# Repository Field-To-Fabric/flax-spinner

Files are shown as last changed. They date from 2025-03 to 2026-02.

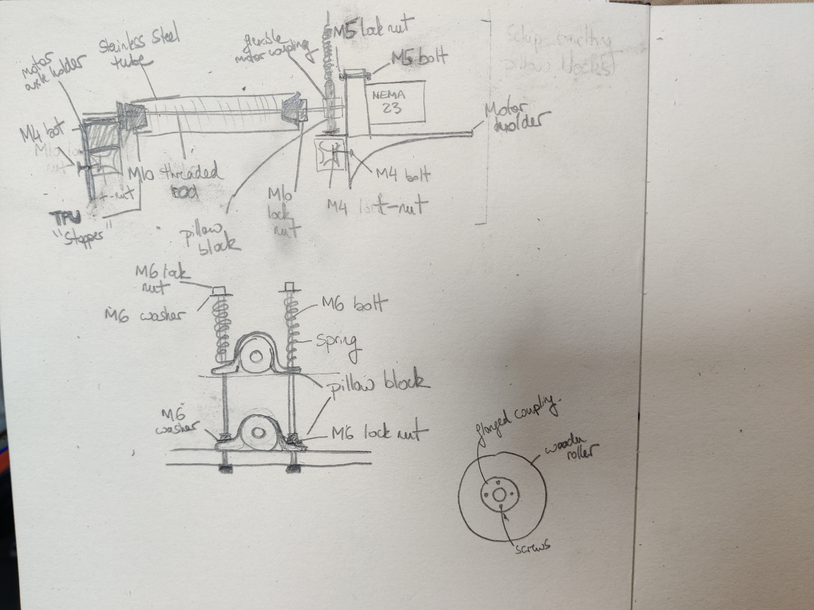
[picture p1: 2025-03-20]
sketches/roller_assembly.jpg

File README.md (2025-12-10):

# flax-spinner
Fantasy Fibre Mill's Flax Spinning Machine

## Materials

These are the materials necessary for building the machine.

### Hardware

For the frame:

* 2 x Aluminium Extrusion bars (30mm * 60 * 1300)
* Aluminium extrusion bars (30mm * 30) - 3 meters
* M4 T-nuts
* M6 T-nuts
* Angle brackets (that can be placed along as well as across the bars)
* M4 nuts and bolts and washers
* M3 nuts and bolts and washers
* M8 lock nuts

For the gill box:

* 2 x NEMA 23 stepper motor (4A, >2.5NM torque, M8 shaft if possible or larger) and stepper motor driver (TB6600)
* 4 x MOD 1.5 50 tooth spur gears ([technobots](https://www.technobotsonline.com/tbot-steel-spur-gear-mod-1.5-50-tooth-ss15-50b.html)). Order with 15mm bore and tapped grub screw holes (pair of M6).
* 4 x 15mm diameter steel round bar, 420mm ([metals4u](https://www.metals4u.co.uk/materials/stainless-steel/stainless-steel-round/1151-p))
* 4 * 15mm diameter steel round bar, 200mm
* 1 x 15mm diameter steel round bar, 250mm
* 2 x 10mm diameter steel round bar, 150mm
* 1 x 8mm diameter steel round bar, 250mm
* 32 x 2.5mm diameter steel round bar, 100mm
* 2 x 2.5mm diamter steel round bar, 150mm
* 2 x 2 bolt flanged bearings, 10mm bore
* 2 x 2 bolt flanged bearings, 15mm bore
* 2 x linear ball bearings for 8mm shaft
* 1 x 10mm bore flanged shaft coupling
* 1 x 8mm bore flanged shaft coupling
* 1 x 10mm to 15mm rigid shaft coupling
* 2 x 8mm to 15mm rigid shaft coupling (this is for stepper motors with 8mm shaft)
* 12 x ball bearing, 15 x 32 x 9 (ID, OD, W)
* 4 x M15 shaft collar
* 2 part epoxy glue
* Assorted M8 bolts with washers
* M8 lock nuts
* M6 T-nuts
* Assorted M6 bolts with washers
* 1 x 10mm bore 1108 taper bush ([bearing boys](https://www.bearingboys.co.uk/1108-Taper-Bushes/110810-Dunlop-Taper-Bush-with-10mm-Bore-2217-p))
* 1 x 15mm bore 1108 taper bush ([bearing boys](https://www.bearingboys.co.uk/1108-Taper-Bushes/110815-Dunlop-Taper-Bush-with-15mm-Bore-136781-p))
* 1 x 15mm bore 2012 taper bush ([bearing boys](https://www.bearingboys.co.uk/2012-Taper-Bushes/201215-Taper-Bush-Dunlop-344374-p)])
* 2 x 28 tooth 8M taperlock pulley (1108 taper bush, 20mm wide belt) ([bearing boys](https://www.bearingboys.co.uk/8M-Taperlock-Timing-Pulley/288M20-Taperlock-Timing-Pulley-21477-p))
* 1 x 56 tooth 8M taperlock pulley (2012 taper bush, 20mm wide belt)([bearing boys](https://www.bearingboys.co.uk/8M-Taperlock-Timing-Pulley/568M20-Taperlock-Timing-Pulley-21486-p))
* 1 x 8M timing belt, 1040mm, 130 teeth, 20mm wide ([bearing boys](https://www.bearingboys.co.uk/8M-Section-8mm-Pitch/10408M20-Timing-Belt-6249-p))

For the rollers:
* 3 x NEMA 23 stepper motor (4A, >2.5NM torque, M8 shaft if possible) and stepper motor driver (TB6600)
* 5 x linen spinning cot (order from Fantasy Fibre Mill)
* M4 T-nuts
* M4 bolts
* 12 x KP000 pillow block bearing, 10mm bore
* 12 x M6 120mm bolt
* 36 x M6 washers (get more to be sure)
* M6 lock nut
* M5 bolts and lock nuts
* M10 lock nut
* 2 x M10 threaded rod 500mm
* 1 x M10 threaded rod 300mm
* 2 x M10 steel rod 500mm
* 1 x M10 steel rod 300mm
* 12 x compression spring, 45mm x 9.6mm, 10.4N/mm (or similar, must fit over M6 bolt)
* 30 x M3 heat inserts
* 30 x M3 bolt, 10mm
* Small wood screws
* 3 x flexible shaft coupling, 10mm to motor shaft size (eg 10 to 8)
* 10 x M10 t-nut with 3 m3 holes (on [amazon](https://www.amazon.co.uk/dp/B0F5PHMNQV?ref_=ppx_hzsearch_conn_dt_b_fed_asin_title_3&th=1))
* 10 x M10 collars (for 10mm steel bar)

For the faller bars:
* 2 x 2.5mm x 200mm steel rods (for each faller bar)
* Gill pin insert (order from Fantasy Fibre Mill).

Electronics:
* 2 x Arduino Mega
* Barrel jack connector
* 24V power supply
* 24V to 12V buck converter

## 3D printing

PLA components:
* One of each gill screw component
* 2 x gill box axle support LHS
* 2 x gill box axle support RHS
* 1 x gill box motor axle support LHS
* 1 x gill box motor axle support RHS
* 5 x drive wheel fine tooth
* 4 x axle mid support
* 3 x motor axle holder
* 3 x motor holder
* 2 x spindle with slot
* 2 x modified ring
* 2 x elevator faller bar blocker
* 2 x elevator faller bar presser
* 2 x elevator guide support holder
* 2 x elevator guide support attachment
* 1 x elevator spring support right
* 1 x elevator spring support left
* For each faller bar print each part once (one full machine takes 29 faller bars)

TPU components (medium shore):
* 10 x cot inserts

## Instructions

Coming soon on our website.

## Contributors
* Iris Veentjer (3D models for gill box elevator)

## License

All source files in this repository are covered by the CERN-OHL-S v2 (even where not explicitly stated). Assume the following license statement applies:

> Copyright Fantasy Fibre Mill 2024.
> This source describes Open Hardware and is licensed under the CERN-
> OHL-S v2.
> You may redistribute and modify this source and make products using it
> under the terms of the CERN-OHL-S v2
> (https://ohwr.org/cern ohl s v2.txt).
> This source is distributed WITHOUT ANY EXPRESS OR IMPLIED
> WARRANTY, INCLUDING OF MERCHANTABILITY, SATISFACTORY
> QUALITY AND FITNESS FOR A PARTICULAR PURPOSE. Please see
> the CERN-OHL-S v2 for applicable conditions.

> As per CERN-OHL-S v2 section 4, should You produce hardware based
> on this source, You must where practicable maintain the Source Location
> visible on the external case of the Textile Machine or other products you make using
> this source.

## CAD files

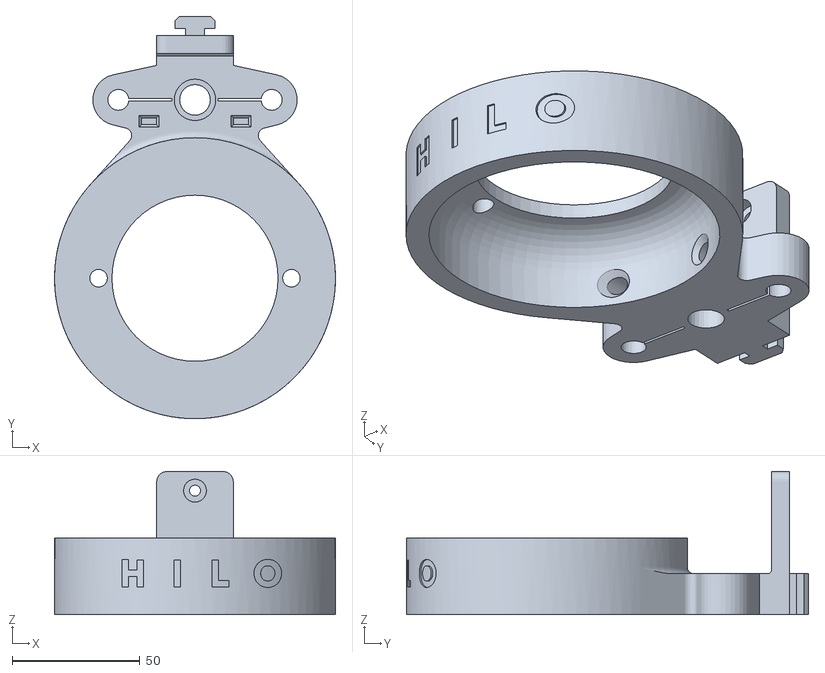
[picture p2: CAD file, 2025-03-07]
parts/PLA/spinning_ring/modified+ring_HILO_Top_Assembly+v14.stl
110.0 x 157.5 x 56.0

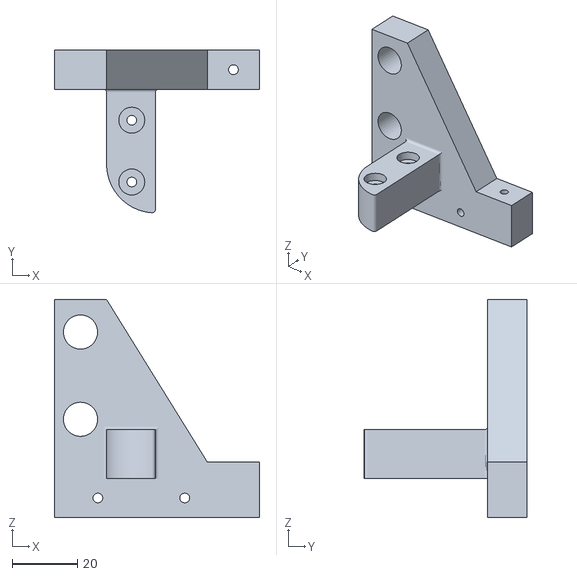
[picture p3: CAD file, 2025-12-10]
parts/PLA/gill_box/elevator/elevator spring support left.stl
63.0 x 50.0 x 67.0

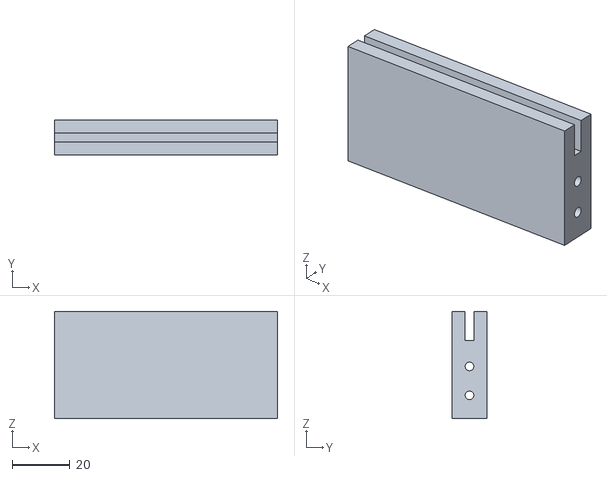
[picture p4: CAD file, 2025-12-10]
parts/PLA/gill_box/faller bar/Faller Bar v3 Middle.stl
77.0 x 12.0 x 37.0

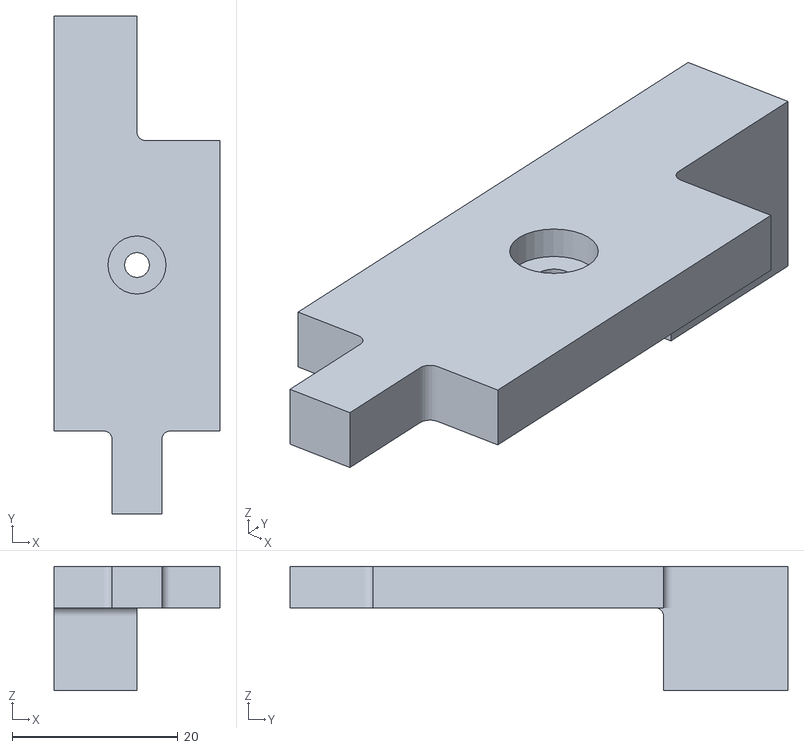
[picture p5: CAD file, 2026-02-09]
parts/PLA/gill_box/Faller_bar_end_guide_RHS_v14.stl
20.0 x 60.0 x 15.0

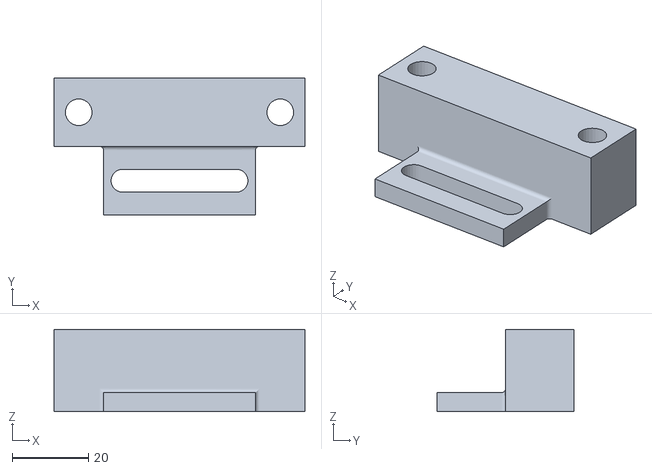
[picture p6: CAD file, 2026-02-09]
parts/PLA/rollers/Middle_Spring_Holder_v16.stl
66.0 x 36.0 x 21.6

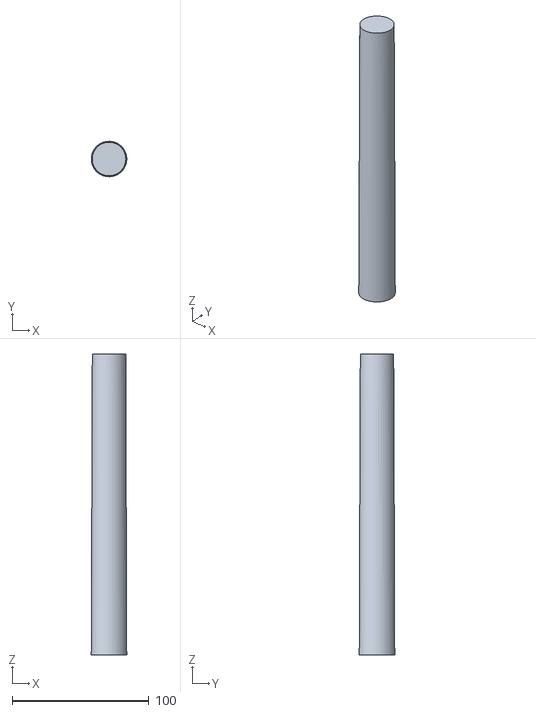
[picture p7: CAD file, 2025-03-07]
parts/PLA/spinning_ring/Spindle+with+slot.stl
26.0 x 26.0 x 220.0

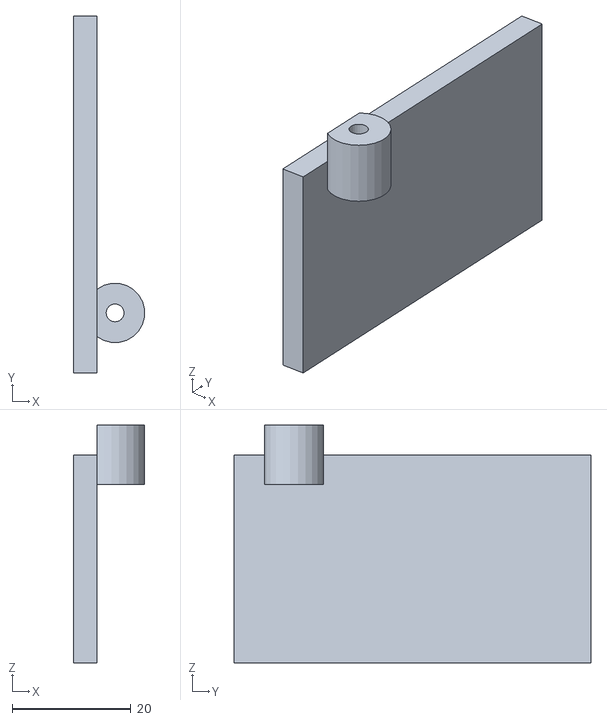
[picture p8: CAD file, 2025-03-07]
parts/PLA/utils/Fibre+Guide(Mirror).stl
12.0 x 60.0 x 40.0

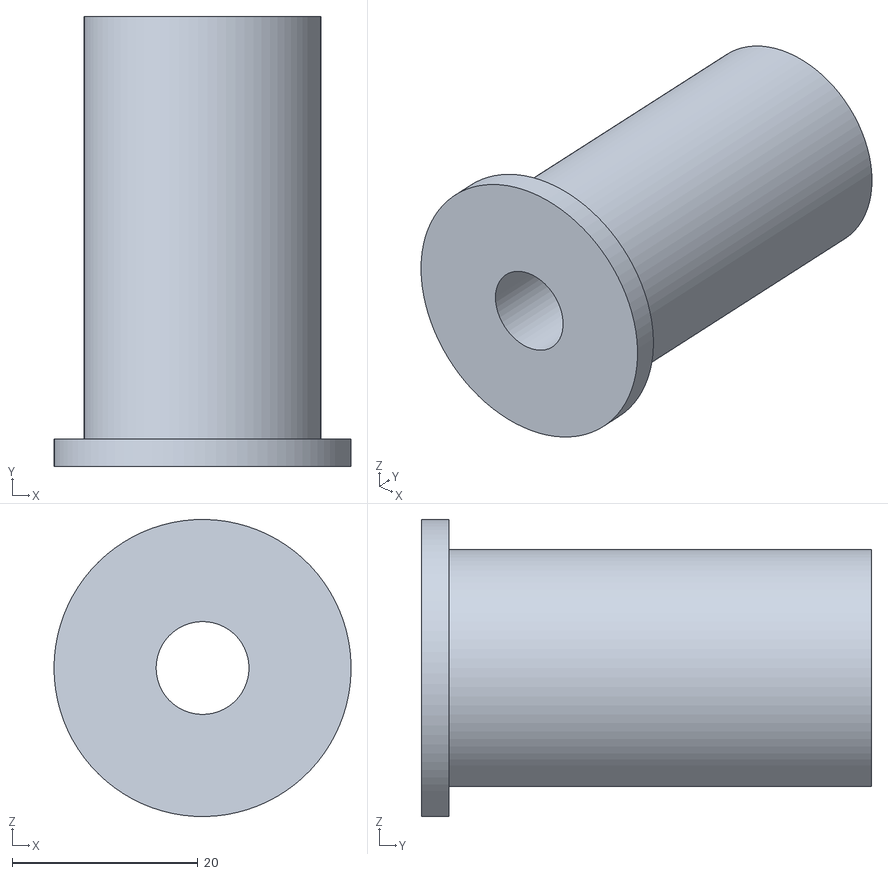
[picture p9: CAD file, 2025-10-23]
parts/TPU/Cot Inserts v1.stl
32.0 x 48.5 x 32.0

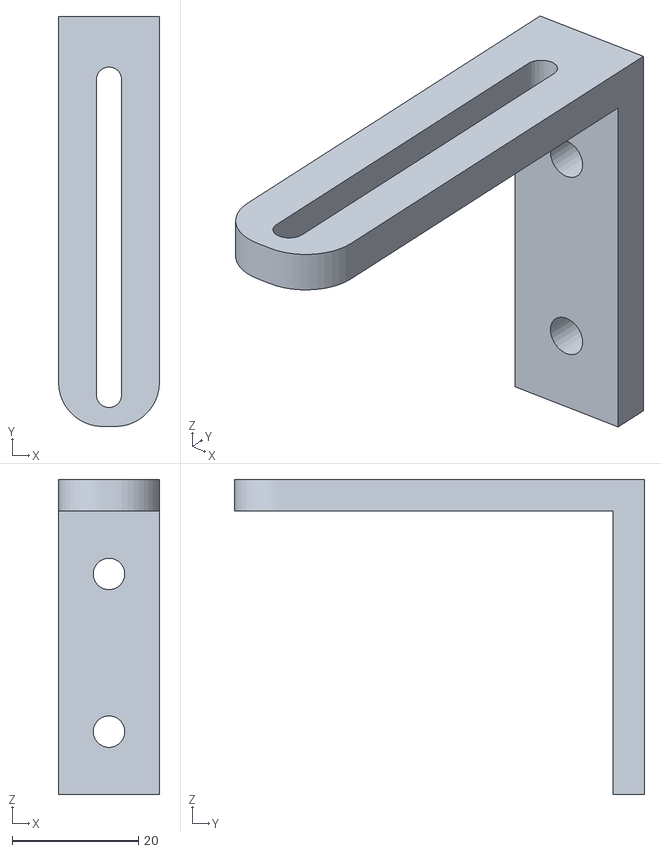
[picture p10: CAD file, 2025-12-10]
parts/PLA/gill_box/elevator/elevator guide support attachment.stl
16.0 x 65.0 x 50.0

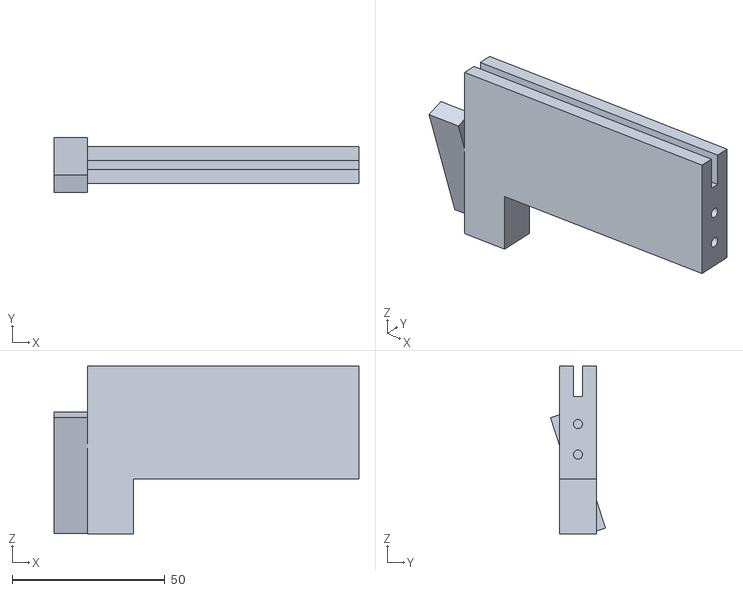
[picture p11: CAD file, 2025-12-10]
parts/PLA/gill_box/faller bar/Faller Bar v4 (Right Side).stl
100.0 x 18.1 x 55.0

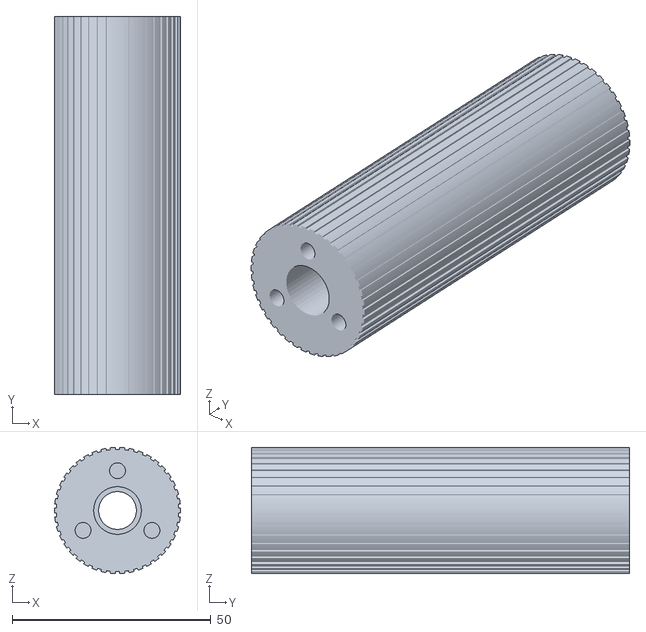
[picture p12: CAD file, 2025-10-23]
parts/PLA/rollers/Drive_wheel_95mm_fine_toothed_v5.stl
31.7 x 95.0 x 31.7

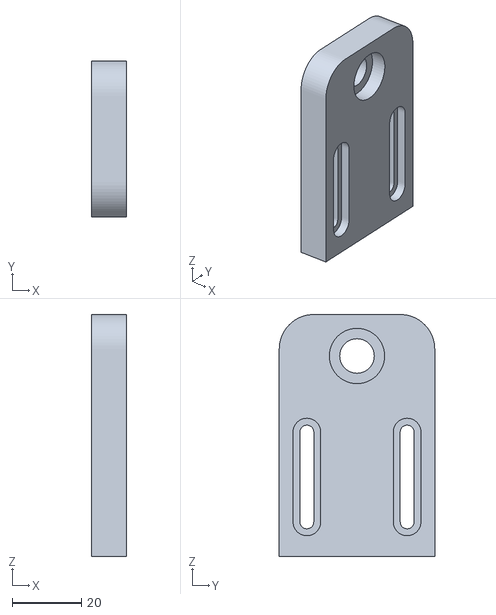
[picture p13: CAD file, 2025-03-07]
parts/PLA/utils/Adjustable Axle Holder v3.stl
10.0 x 45.0 x 70.0

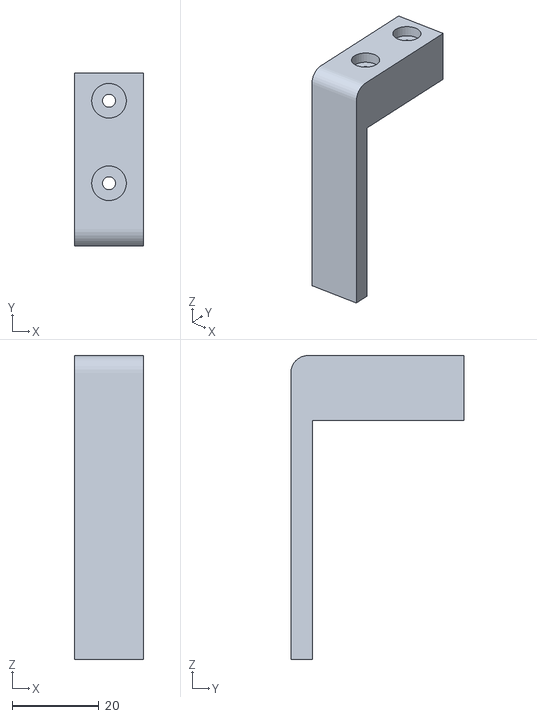
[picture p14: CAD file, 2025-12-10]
parts/PLA/gill_box/elevator/elevator faller bar blocker.stl
16.0 x 39.9 x 70.0

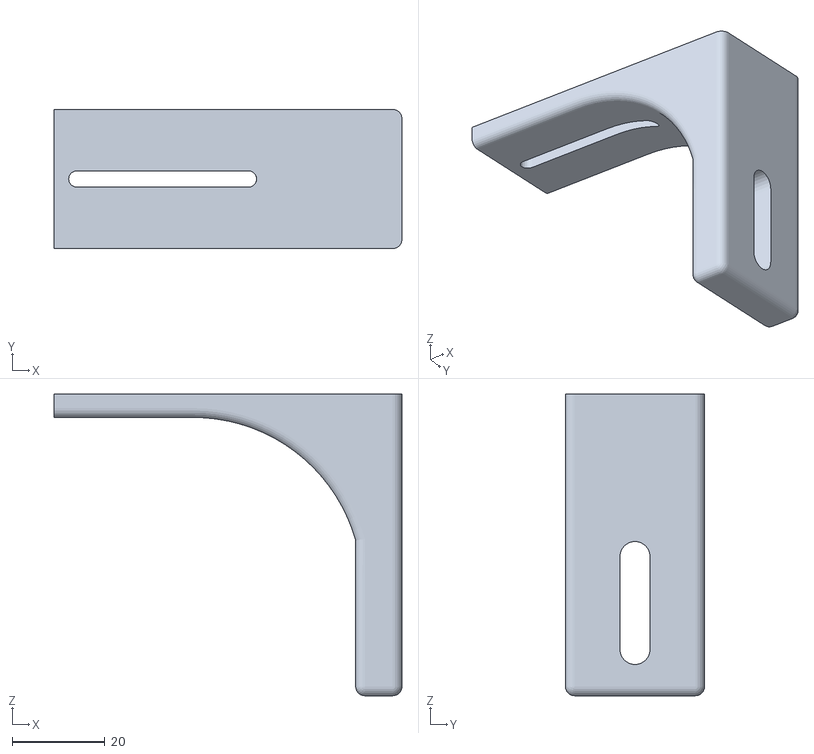
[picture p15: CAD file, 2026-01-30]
parts/PLA/gill_box/Top_slide_support_Gill_Box_Supports_v13.stl
75.0 x 30.0 x 65.0

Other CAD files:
parts/PLA/gill_box/Faller_bar_end_guide_LHS_v14.stl
parts/PLA/gill_box/faller bar/Faller Bar v4 (Left Side).stl
parts/PLA/rollers/Drive_wheel_95mm_wide_toothed_v5.stl
parts/PLA/utils/Adjustable Bracket v15.stl
parts/PLA/gill_box/Gill_Box_Axle_Support_LHS_v9.stl
parts/PLA/gill_box/Gill_Box_Axle_Support_RHS_v9.stl
parts/PLA/gill_box/Gill_Box_Motor_Axle_Support_LHS_v9.stl
parts/PLA/gill_box/Gill_Box_Motor_Axle_Support_RHS_v9.stl
parts/PLA/gill_box/Gill_Box_Top_Slide_Support_v9.stl
parts/PLA/gill_box/Gill_Screw_Bottom_Left_Handed_Part_1_v10.stl
parts/PLA/gill_box/Gill_Screw_Bottom_Left_Handed_Part_2_v10.stl
parts/PLA/gill_box/Gill_Screw_Bottom_Left_Handed_Part_3_v10.stl
parts/PLA/gill_box/Gill_Screw_Bottom_Left_Handed_Part_4_v10.stl
parts/PLA/gill_box/Gill_Screw_Bottom_Left_Handed_Part_5_v10.stl
parts/PLA/gill_box/Gill_Screw_Bottom_Right_Handed_Part_1_v10.stl
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

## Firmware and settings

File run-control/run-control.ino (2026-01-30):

int PHOTO_SWITCH_PIN = 3;

int photoSwitchVal = 0;
// Value is high when the sensor is blocked
long lastSwitchToHigh = 0;
// Value is low when the sensor is not blocked
long lastSwitchToLow = 0;

void setup() {
  Serial.begin(9600);
  pinMode(PHOTO_SWITCH_PIN, INPUT_PULLUP);
}

void loop() {
  if (digitalRead(PHOTO_SWITCH_PIN) == HIGH) {
    if (photoSwitchVal == LOW) {
      // Change detected, LOW to HIGH
      photoSwitchVal = HIGH;
      long now = millis();
      long interval = now - lastSwitchToLow;
      Serial.print("Time since last passage: ");
      Serial.println(interval);
      lastSwitchToHigh = now;
    }
  } else {
    if (photoSwitchVal == HIGH) {
      // Change detected, HIGH to LOW
      photoSwitchVal = LOW;
      long now = millis();
      long interval = now - lastSwitchToHigh;
      Serial.print("Time blocked: ");
      Serial.println(interval);
      lastSwitchToLow = now;
    }
  }
}

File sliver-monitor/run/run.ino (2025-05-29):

/*
 Example using the SparkFun HX711 breakout board with a scale
 By: Nathan Seidle
 SparkFun Electronics
 Date: November 19th, 2014
 License: This code is public domain but you buy me a beer if you use this and we meet someday (Beerware license).

 This example demonstrates basic scale output. See the calibration sketch to get the calibration_factor for your
 specific load cell setup.

 This example code uses bogde's excellent library:"https://github.com/bogde/HX711"
 bogde's library is released under a GNU GENERAL PUBLIC LICENSE

 The HX711 does one thing well: read load cells. The breakout board is compatible with any wheat-stone bridge
 based load cell which should allow a user to measure everything from a few grams to tens of tons.
 Arduino pin 2 -> HX711 CLK
 3 -> DAT
 5V -> VCC
 GND -> GND

 The HX711 board can be powered from 2.7V to 5V so the Arduino 5V power should be fine.

*/

#include "HX711.h"

#define calibration_factor -406.0 //This value is obtained using the SparkFun_HX711_Calibration sketch

#define LOADCELL_DOUT_PIN  3
#define LOADCELL_SCK_PIN  4

HX711 scale;

float minChange = 0.5f;
long minChangeMs = 700;
float lastReading;
long lastReadingMillis = 0;
long totalStoppage = 0;
long pauseDetectionTimer = 0;
boolean pauseTimerActivated = false;


void setup() {
  Serial.begin(9600);

  scale.begin(LOADCELL_DOUT_PIN, LOADCELL_SCK_PIN);
  scale.set_scale(calibration_factor); //This value is obtained by using the SparkFun_HX711_Calibration sketch
  scale.tare(); //Assuming there is no weight on the scale at start up, reset the scale to 0
}

void loop() {
  long currentMillis = millis();
  Serial.print(currentMillis);
  Serial.print(",");
  float reading = scale.get_units(5);
  Serial.print(reading, 1); //scale.get_units() returns a float
  Serial.println();
  lastReading = reading;
  lastReadingMs = currentMillis;
  handleSerialInput();
}

void handleSerialInput() {
  if(Serial.available()) {
    char temp = Serial.read();
    if (temp == 't') {
      scale.tare();
    }
  } 
}

// Pause detection algorithm
// Sample readings every X milliseconds. If more than 3 samples in a row return values within a range than we have a pause.
// Once one reading is out of the pause range then start again.

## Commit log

2025-03-06 Adding materials for flax spinner.
2025-03-07 Parts for flax spinner.
    [Adjustable Axle Holder v3(1)(1).stl, Adjustable Bracket v15.stl, Fibre+Fork.stl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]
2025-03-12 Uploading TPU model and reorganizing models.
    [Adjustable Axle Holder v3(1)(1).stl, Adjustable Bracket v15.stl, Fibre+Fork.stl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]
2025-03-12 Correcting model organization.
    [Adjustable Axle Holder v3.stl, Spindle+with+slot.stl, Tapered+Pipe+insert_10mm.stl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]
2025-03-20 Adding roller assembly sketch.
2025-10-23 Updating models and adding models for gill box.
    [Adjustable Axle Holder v3.stl, Adjustable Bracket v15.stl, Cot Inserts v1.stl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]
2025-11-14 Adding comment about spring strength.
2025-12-10 Adding faller bar and gill box elevator models.
    [Faller Bar v3 Middle.stl, Faller Bar v4 (Left Side).stl, Faller Bar v4 (Right Side).stl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]
2026-01-30 Updating top slide support model
    [Top_slide_support_Gill_Box_Supports_v12.stl, Top_slide_support_Gill_Box_Supports_v13.stl]
2026-02-09 Added faller bar end models and middle spring holder model.
    [Faller_bar_end_guide_LHS_v14.stl, Faller_bar_end_guide_RHS_v14.stl, Middle_Spring_Holder_v16.stl]
